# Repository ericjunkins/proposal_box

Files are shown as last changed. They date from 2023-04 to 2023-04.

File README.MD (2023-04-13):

# Proposal Box

<p float="left">
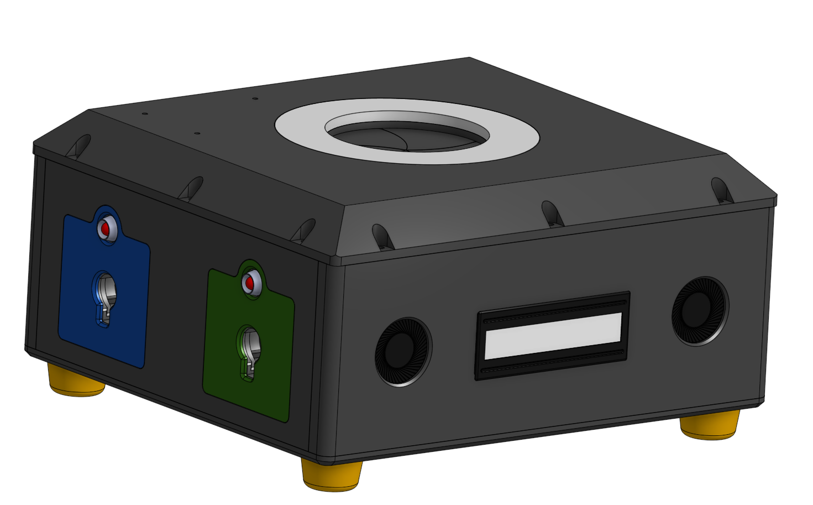
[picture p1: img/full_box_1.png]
  
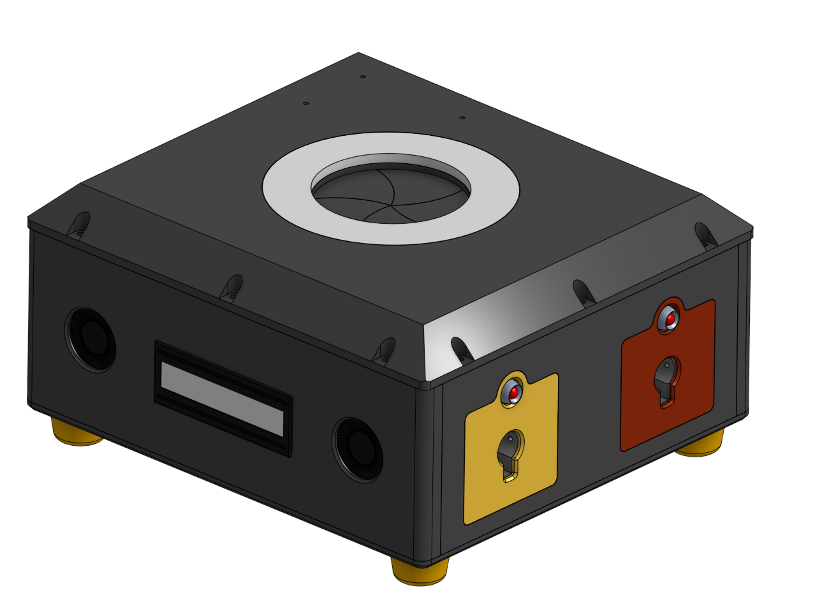
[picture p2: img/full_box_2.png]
   
</p>

<p float="left">
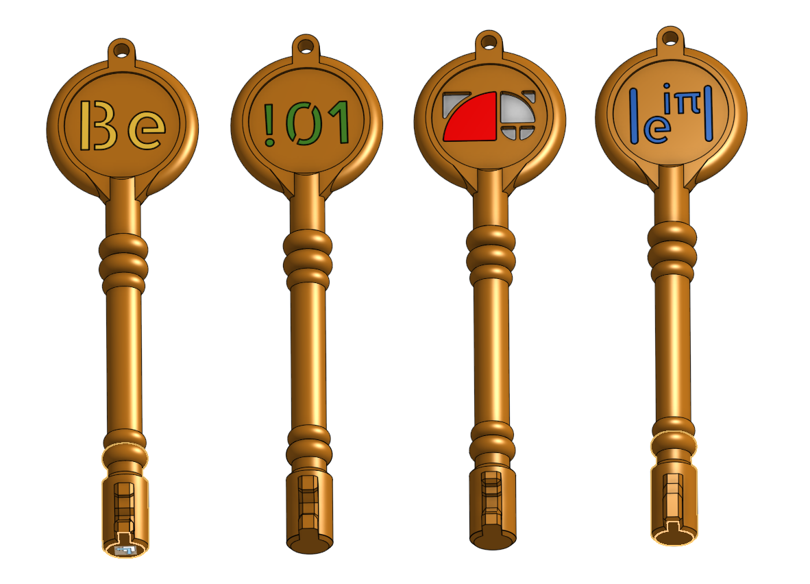
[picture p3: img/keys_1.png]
  
</p>

## Electrical Design

The design consists of 3 custom PCBs, alongside a set of electrical and mechanical parts to accomplish the motion, and user interaction desired.

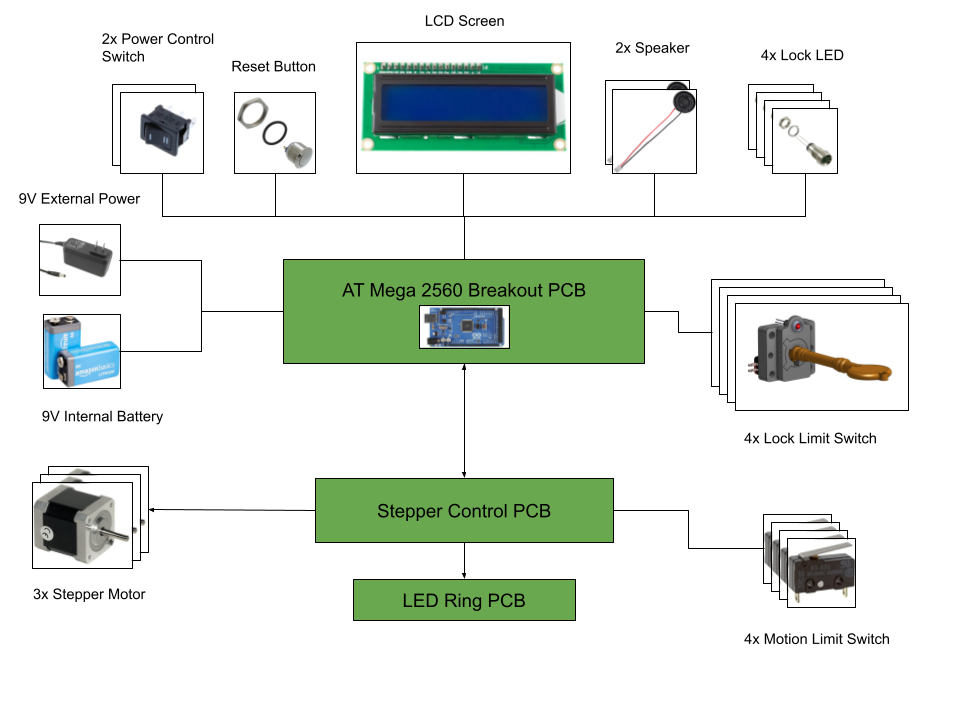
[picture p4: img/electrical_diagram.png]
Electrical Diagram


Full schematics, gerber files, and design files can be found in [electrical design folder](electrical_design/)
<p float="left">
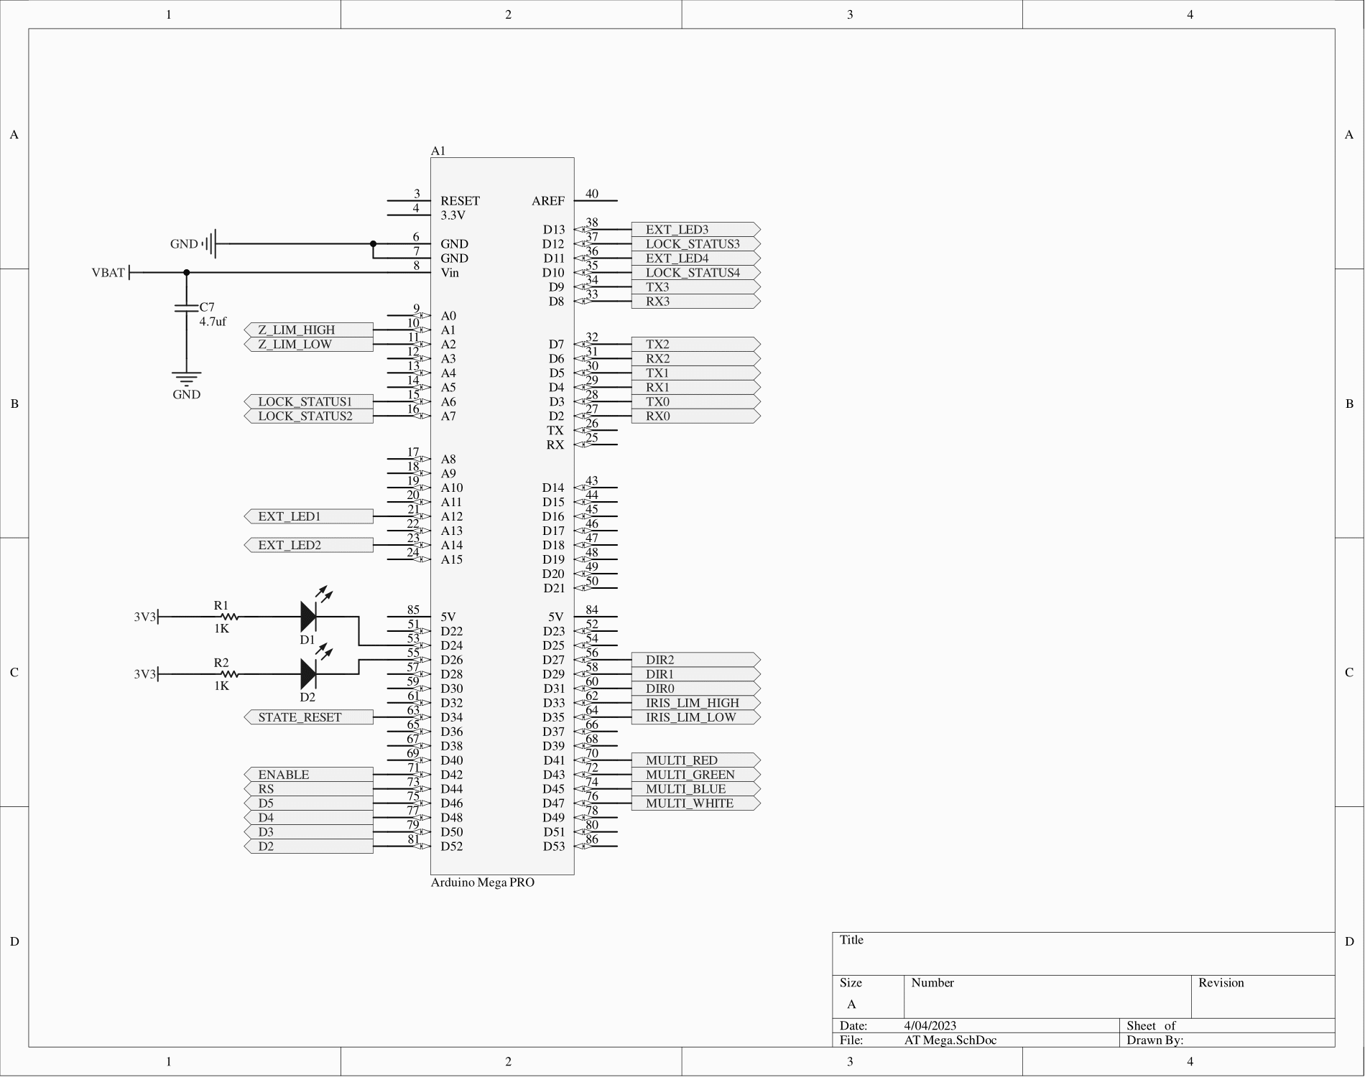
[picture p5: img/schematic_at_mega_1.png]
  
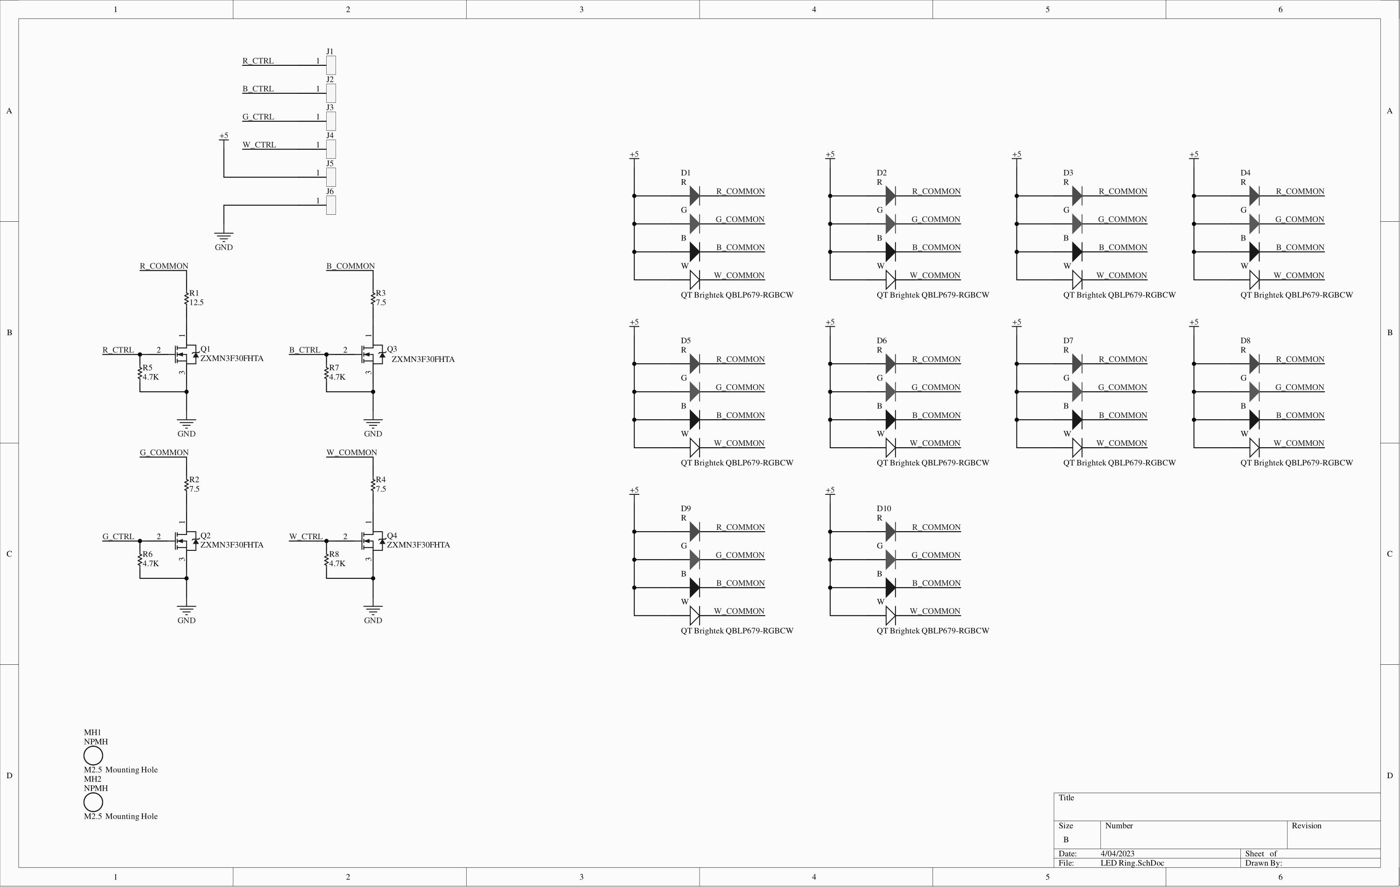
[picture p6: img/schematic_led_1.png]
   
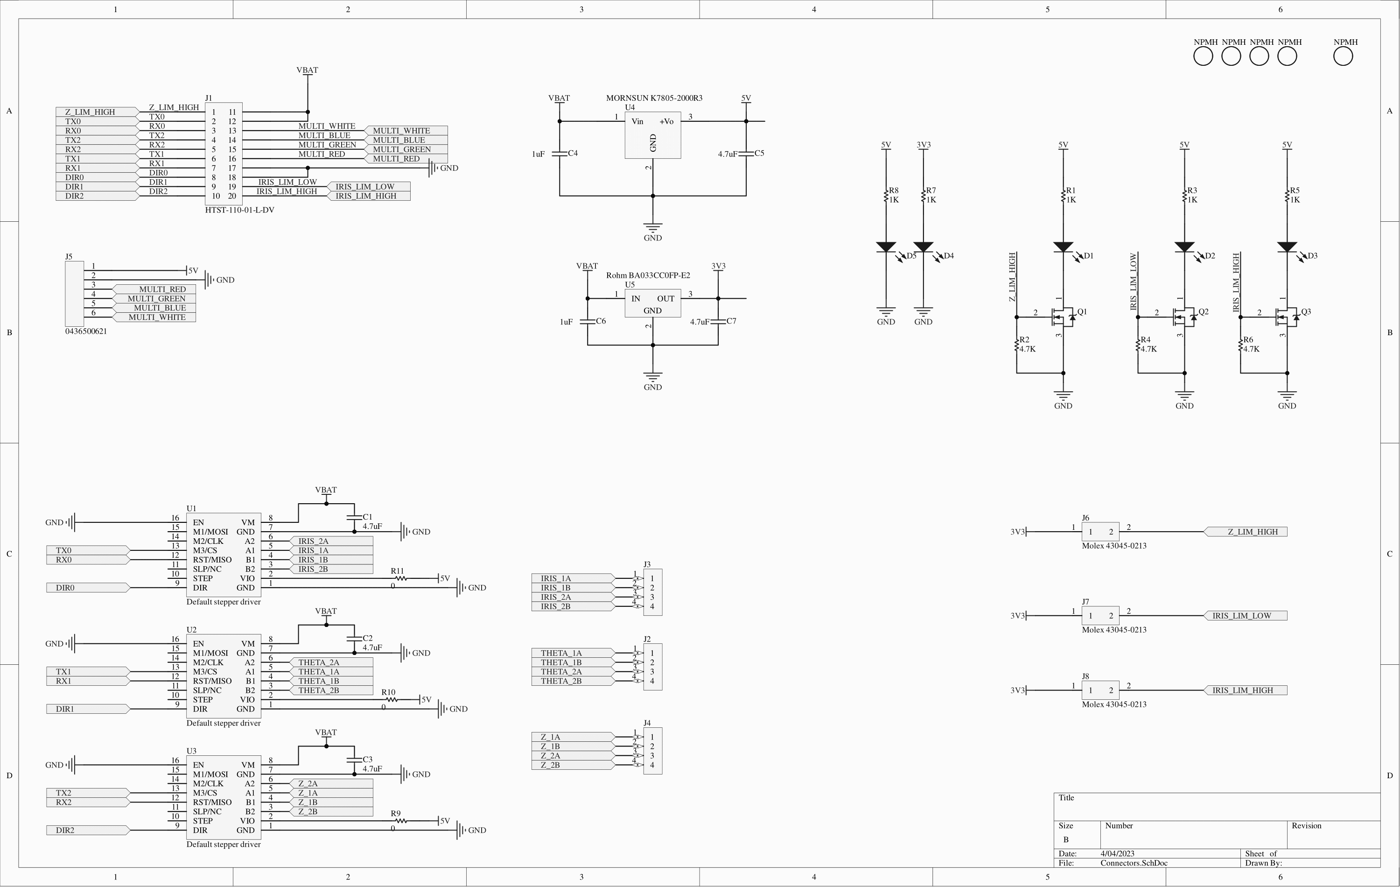
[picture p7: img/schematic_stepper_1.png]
   
</p>

## Mechanical Design

The CAD design of the project can be found at: https://cad.onshape.com/documents/44e33e8e96f078937c0840d5/w/a803ee7c0c0ba1d54d61a190/e/53a78a30a7107b3de1d018e0

### Structure

<p float="left">
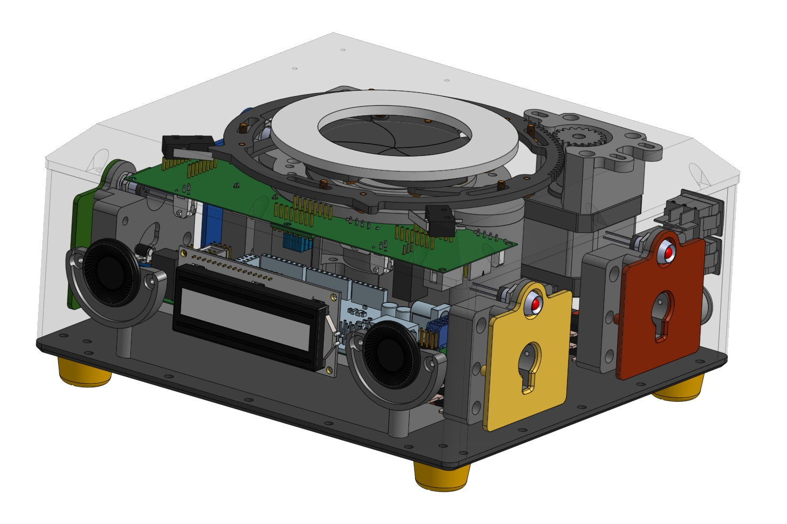
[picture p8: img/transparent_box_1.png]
  
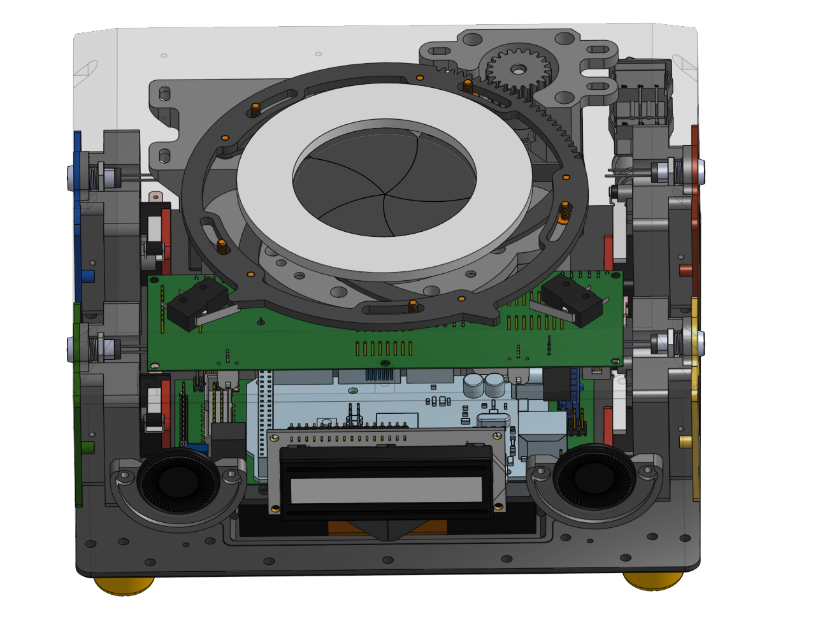
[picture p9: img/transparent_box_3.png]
   
</p>

## Iris
<p float="left">
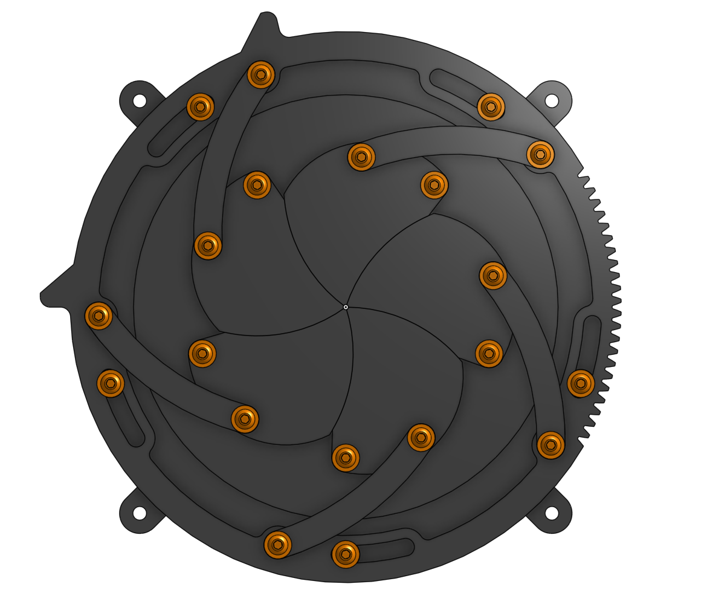
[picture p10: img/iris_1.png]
  
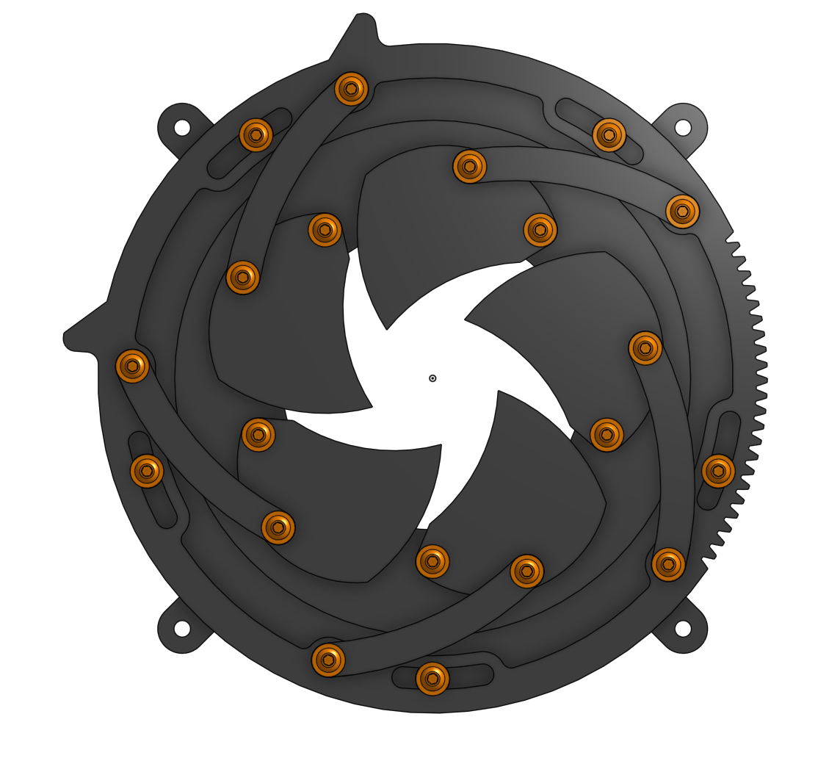
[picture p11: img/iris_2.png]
   
</p>

## Locks

<p float="left">
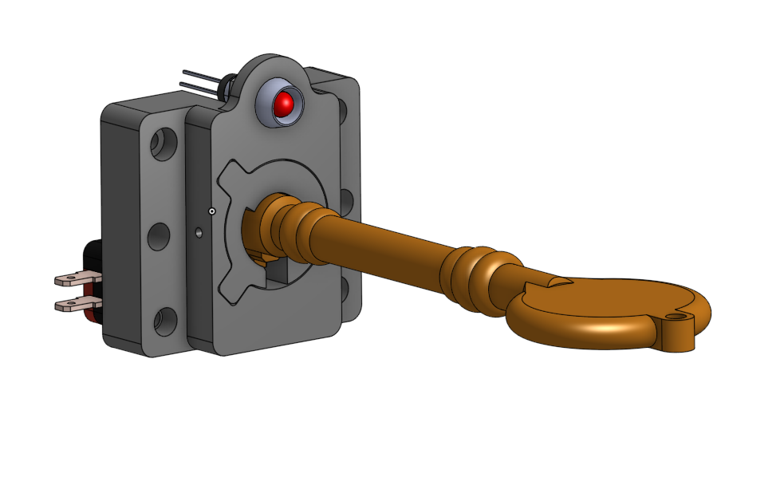
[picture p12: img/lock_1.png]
  
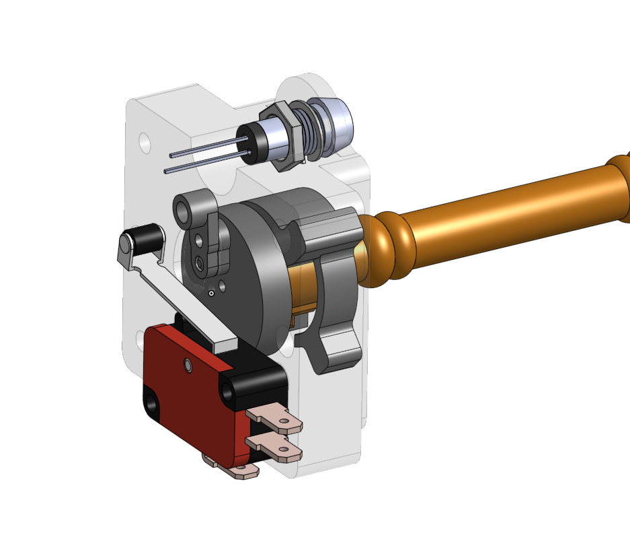
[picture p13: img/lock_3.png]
   
</p>

## BOM

Bill of Materials can be found in the [BOM Folder](BOM/)

## Software

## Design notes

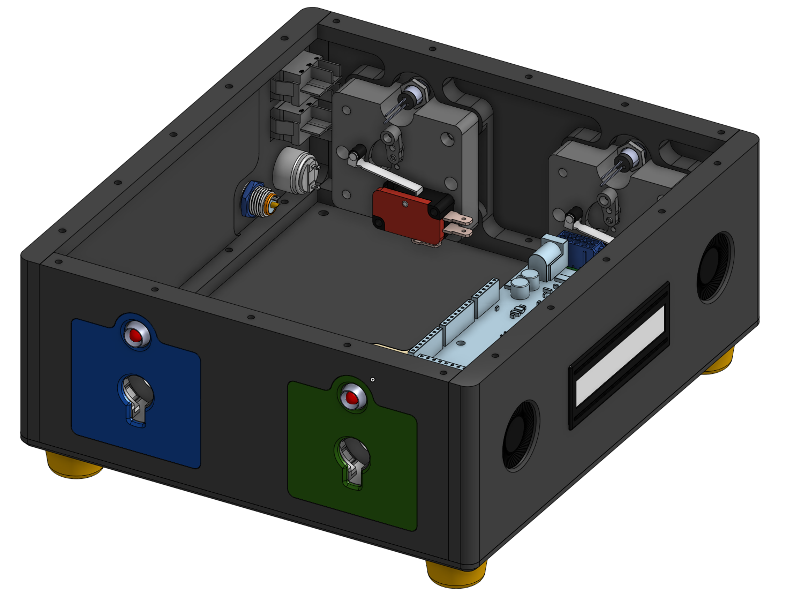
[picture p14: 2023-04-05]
img/bottom_2.png

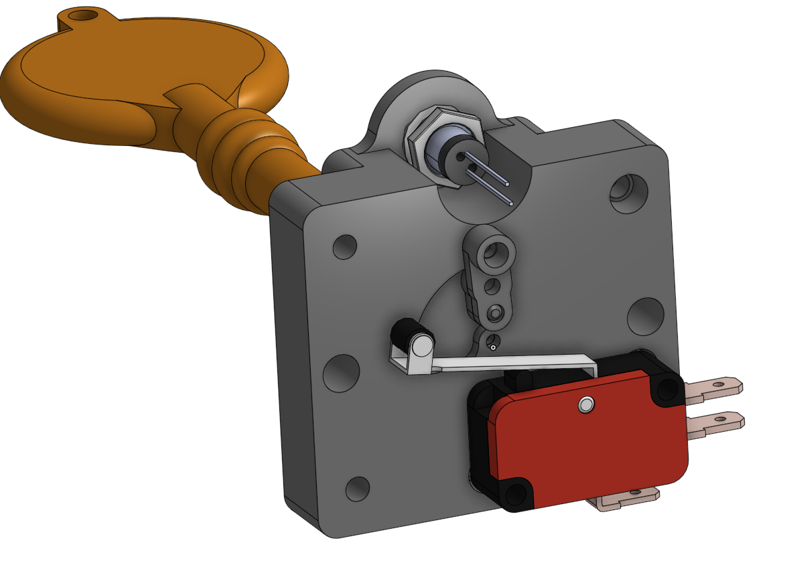
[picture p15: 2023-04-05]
img/lock 2.png

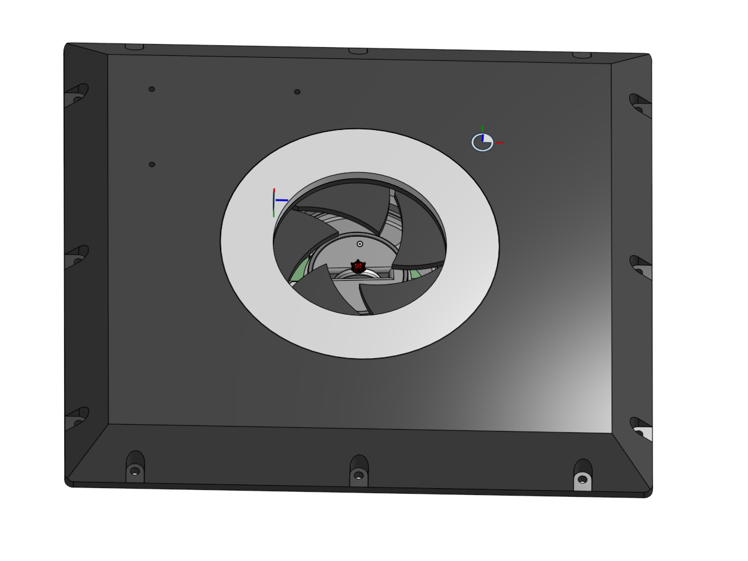
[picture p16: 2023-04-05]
img/lid_3.png

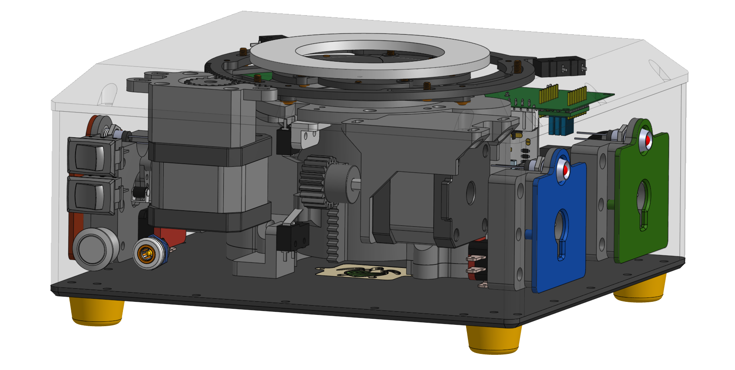
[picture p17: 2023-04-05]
img/transparent_box_2.png

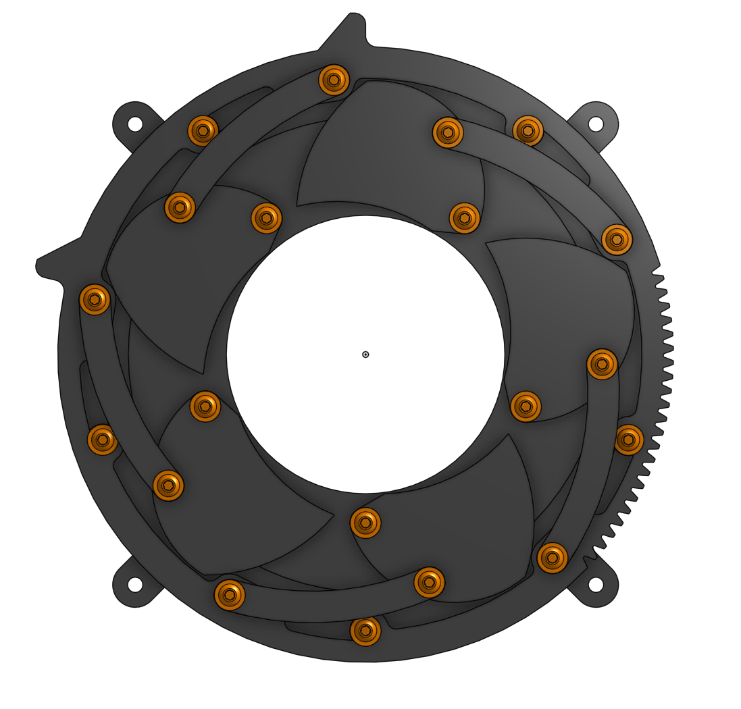
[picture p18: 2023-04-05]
img/iris_3.png

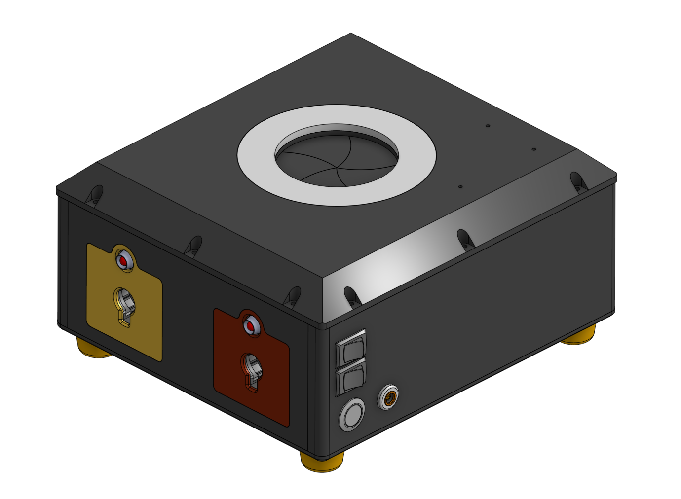
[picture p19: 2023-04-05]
img/full_box_3.png

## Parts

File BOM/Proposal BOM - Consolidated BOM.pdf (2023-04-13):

Part Type | Vendor | Quantity Part Number | Manufacturer Part Number Description | Customer Reference | Unit Price | Extended Price USD | Material | Finish | Color | Link PCB | Digikey | 10 ZXMN3F30FHCT-ND | ZXMN3F30FHTA | MOSFET N-CH 30V 3.8A SOT23-3 | Q1, Q2, Q3, Q4 | $0.47 | $4.70 N/A | N/A | N/A | N/A
PCB | Digikey | 10 1516-QBLP679-RGBCWCT-ND QBLP679-RGBCW | LED RGBW DIFFUSED 8PLCC SMD
D1, D2, D3, D4, D5, D6, D7, D8, D9, D10 | $0.49 | $4.93 N/A | N/A | N/A | N/A
PCB | Digikey | 10 A130138CT-ND | CRGCQ0805J4K7 | RES 4.7K OHM 5% 1/8W 0805 | R1, R2, R3, R4 | $0.04 | $0.38 N/A | N/A | N/A | N/A
PCB | Digikey | 10 A130132CT-ND | CRGCQ0805J470R | RES 470 OHM 5% 1/8W 0805 | R5, R6, R7, R8 | $0.03 | $0.32 N/A | N/A | N/A | N/A
PCB | Digikey | 1 SAM10529-ND | HTST-110-01-L-DV | CONN HEADER SMD 20POS 2.54MM | J1 | $4.37 | $4.37 N/A | N/A | N/A | N/A
PCB | Digikey | 1 WM20166CT-ND | 0436500621 | CONN HEADER SMD 6POS 3MM | J5 | $3.33 | $3.33 N/A | N/A | N/A | N/A
PCB | Digikey | 1 2725-K7805-2000R3-ND | K7805-2000R3 | DC DC CONVERTER 5V 10W | U4 | $7.11 | $7.11 N/A | N/A | N/A | N/A
PCB | Digikey | 1 BA033CC0FP-E2CT-ND | BA033CC0FP-E2 | IC REG LINEAR 3.3V 1A TO252-3 | U5 | $1.41 | $1.41 N/A | N/A | N/A | N/A
PCB | Digikey | 6 SSW-108-01-T-S-LL-ND | SSW-108-01-T-S-LL | CONN RCPT 8POS 0.1 TIN PCB | U1, U2, U3 | $1.47 | $8.82 N/A | N/A | N/A | N/A
PCB | Digikey | 3 WM1919-ND | 0436500415 | CONN HEADER VERT 4POS 3MM | J2, J3, J4 | $1.28 | $3.84 N/A | N/A | N/A | N/A
PCB | Digikey | 3 WM2648-ND | 0430450213 | CONN HEADER VERT 2POS | J6, J7, J8 | $1.21 | $3.63 N/A | N/A | N/A | N/A
PCB | Digikey | 3 ZXMN3F30FHCT-ND | ZXMN3F30FHTA | MOSFET N-CH 30V 3.8A SOT23-3 | Q1, Q2, Q3 | $0.47 | $1.41 N/A | N/A | N/A | N/A
PCB | Digikey | 10 A130138CT-ND | CRGCQ0805J4K7 | RES 4.7K OHM 5% 1/8W 0805 | R1, R3, R5, R7, R8 | $0.04 | $0.38 N/A | N/A | N/A | N/A
PCB | Digikey | 10 A130132CT-ND | CRGCQ0805J470R | RES 470 OHM 5% 1/8W 0805 | R2, R4, R6 | $0.03 | $0.32 N/A | N/A | N/A | N/A
PCB | Digikey | 10 RMCF0805ZT0R00CT-ND | RMCF0805ZT0R00 | RES 0 OHM JUMPER 1/8W 0805 | R9, R10, R11 | $0.02 | $0.18 N/A | N/A | N/A | N/A
PCB | Digikey | 10 1276-1244-1-ND | CL21A475KAQNNNE | CAP CER 4.7UF 25V X5R 0805 | C1, C2, C3, C5, C7 | $0.07 | $0.73 N/A | N/A | N/A | N/A
PCB | Digikey | 10 1276-1066-1-ND | CL21B105KAFNNNE | CAP CER 1UF 25V X7R 0805 | C4, C6 | $0.07 | $0.65 N/A | N/A | N/A | N/A
PCB | Digikey | 10 160-1423-1-ND | LTST-C171GKT | LED GREEN CLEAR CHIP SMD | D1, D2, D3, D4, D5 | $0.14 | $1.41 N/A | N/A | N/A | N/A
PCB | Digikey | 10 A130135CT-ND | CRGCQ0805J1K5 | RES 1.5K OHM 5% 1/8W 0805 | R1, R2, R3, R4, R5 | $0.04 | $0.38 N/A | N/A | N/A | N/A
PCB | Digikey | 10 13-RC0805FR-13220RLCT-ND RC0805FR-13220RL | RES 220 OHM 1% 1/8W 0805 | R10, R12, R16, R17, R21 | $0.03 | $0.25 N/A | N/A | N/A | N/A
PCB | Digikey | 10 A130138CT-ND | CRGCQ0805J4K7 | RES 4.7K OHM 5% 1/8W 0805
R6, R7, R8, R9, R13, R14, R15, R18, R19, R22 | $0.04 | $0.38 N/A | N/A | N/A | N/A
PCB | Digikey | 10 RMCF0805ZT0R00CT-ND | RMCF0805ZT0R00 | RES 0 OHM JUMPER 1/8W 0805 | C5, C6 | $0.02 | $0.18 N/A | N/A | N/A | N/A
PCB | Digikey | 10 1276-1066-1-ND | CL21B105KAFNNNE | CAP CER 1UF 25V X7R 0805 | C1, C3, C8, C10 | $0.07 | $0.65 N/A | N/A | N/A | N/A
PCB | Digikey | 10 1276-1244-1-ND | CL21A475KAQNNNE | CAP CER 4.7UF 25V X5R 0805 | C7, C9, C11 | $0.07 | $0.73 N/A | N/A | N/A | N/A
PCB | Digikey | 10 1276-1096-1-ND | CL21A106KOQNNNE | CAP CER 10UF 16V X5R 0805 | C2, C4 | $0.07 | $0.74 N/A | N/A | N/A | N/A
PCB | Digikey | 10 160-1423-1-ND | LTST-C171GKT | LED GREEN CLEAR CHIP SMD | D1, D2, D3, D4 | $0.14 | $1.41 N/A | N/A | N/A | N/A
PCB | Digikey | 1 1738-1041-ND | DFR0299 | DFPLAYER - A MINI MP3 PLAYER | U1 | $5.90 | $5.90 N/A | N/A | N/A | N/A
PCB | Digikey | 1 PAM8406DRDICT-ND | PAM8406DR | IC AMP D/AB STEREO 5W 16SOP | U2 | $0.85 | $0.85 N/A | N/A | N/A | N/A
PCB | Digikey | 1 WM1793-ND | 0430451012 | CONN HEADER VERT 10POS 3MM | J13 | $2.60 | $2.60 N/A | N/A | N/A | N/A
PCB | Digikey | 1 2725-K7805-2000R3-ND | K7805-2000R3 | DC DC CONVERTER 5V 10W | U3 | $7.11 | $7.11 N/A | N/A | N/A | N/A
PCB | Digikey | 1 BA033CC0FP-E2CT-ND | BA033CC0FP-E2 | IC REG LINEAR 3.3V 1A TO252-3 | U4 | $1.41 | $1.41 N/A | N/A | N/A | N/A
PCB | Digikey | 1 2057-PH1-12-UA-ND | PH1-12-UA | CONN HEADER VERT 12POS 2.54MM | J12 | $0.20 | $0.20 N/A | N/A | N/A | N/A
PCB | Digikey | 2 SAM8996-ND | TSW-104-07-F-D | CONN HEADER VERT 8POS 2.54MM | J5, J7 | $0.97 | $1.94 N/A | N/A | N/A | N/A
PCB | Digikey | 3 732-5315-ND | 61300211121 | CONN HEADER VERT 2POS 2.54MM | J1, J2, J9 | $0.13 | $0.39 N/A | N/A | N/A | N/A
PCB | Digikey | 1 SAM10529-ND | HTST-110-01-L-DV | CONN HEADER SMD 20POS 2.54MM | J6 | $4.37 | $4.37 N/A | N/A | N/A | N/A
PCB | Digikey | 2 1034-ZXMN3F31DN8CT-ND | ZXMN3F31DN8TA | MOSFET 2N-CH 30V 5.7A 8SOIC | Q1, Q2 | $0.87 | $1.74 N/A | N/A | N/A | N/A
PCB | Digikey | 1 1050-1018-ND | A000067 | ARDUINO MEGA2560 ATMEGA2560 | A1 | $48.40 | $48.40 N/A | N/A | N/A | N/A
PCB | Digikey | 1 2553-2044-2X18G00SA-ND | 2044-2X18G00SA | PCB SOCKET, DOUBLE ROW, 36 PIN, | A1 | $1.00 | $1.00 N/A | N/A | N/A | N/A
PCB | Digikey | 10 SSW-108-01-T-S-LL-ND | SSW-108-01-T-S-LL | CONN RCPT 8POS 0.1 TIN PCB | A1, U2 | $1.28 | $12.82 N/A | N/A | N/A | N/A
PCB | Digikey | 1 CT-9EW103-ND | CT-9EW103 | TRIMMER 10K OHM 0.5W PC PIN TOP | R20 | $2.07 | $2.07 N/A | N/A | N/A | N/A Machine Part | Alibaba | 5 N/A | N/A | Iris_leaf | N/A | $14.00 | $70.00 Aluminum 6061 | Type 2 Annodize | Black | N/A Machine Part | Alibaba | 1 N/A | N/A | Iris_base | N/A | $36.50 | $36.50 Aluminum 6061 | Type 2 Annodize | Black | N/A Machine Part | Alibaba | 1 N/A | N/A | Spur_gear | N/A | $46.50 | $46.50 Aluminum 6061 | Type 2 Annodize | Black | N/A Machine Part | Alibaba | 1 N/A | N/A | Lock_cover | N/A | $21.50 | $21.50 Aluminum 6061 | Type 2 Annodize | Red | N/A Machine Part | Alibaba | 1 N/A | N/A | Lock_cover | N/A | $21.50 | $21.50 Aluminum 6061 | Type 2 Annodize | Blue | N/A Machine Part | Alibaba | 1 N/A | N/A | Lock_cover | N/A | $21.50 | $21.50 Aluminum 6061 | Type 2 Annodize | Green | N/A Machine Part | Alibaba | 1 N/A | N/A | Lock_cover | N/A | $21.50 | $21.50 Aluminum 6061 | Type 2 Annodize | Yellow | N/A Machine Part | Alibaba | 1 N/A | N/A | Back_plate | N/A | $24.00 | $24.00 Aluminum 6061 | Type 2 Annodize | Black | N/A Machine Part | Alibaba | 1 N/A | N/A | Bottom_plate | N/A | $23.00 | $23.00 Aluminum 6061 | Type 2 Annodize | Black | N/A Machine Part | Alibaba | 1 N/A | N/A | Front_plate | N/A | $33.00 | $33.00 Aluminum 6061 | Type 2 Annodize | Black | N/A Machine Part | Alibaba | 1 N/A | N/A | Lid_plate | N/A | $100.00 | $100.00 Aluminum 6061 | Type 2 Annodize | Black | N/A Machine Part | Alibaba | 2 N/A | N/A | Side_plate | N/A | $25.00 | $50.00 Aluminum 6061 | Type 2 Annodize | Black | N/A
3D Printed | JLCPCB | 6 N/A | N/A | Lock Housing - Bar | N/A | $1.00 | $6.00 Black Resin | Sanding | Matte Black | N/A
3D Printed | JLCPCB | 2 N/A | N/A | Key 1 Static | N/A | $1.00 | $2.00 Black Resin | Sanding | Matte Black | N/A
3D Printed | JLCPCB | 2 N/A | N/A | Key 2 Static | N/A | $1.00 | $2.00 Black Resin | Sanding | Matte Black | N/A
3D Printed | JLCPCB | 2 N/A | N/A | Key 3 Static | N/A | $1.00 | $2.00 Black Resin | Sanding | Matte Black | N/A
3D Printed | JLCPCB | 2 N/A | N/A | Key 4 Static | N/A | $1.00 | $2.00 Black Resin | Sanding | Matte Black | N/A
3D Printed | JLCPCB | 5 N/A | N/A | Lock Housing - Tumbler 0 | N/A | $1.00 | $5.00 Black Resin | Sanding | Matte Black | N/A
3D Printed | JLCPCB | 6 N/A | N/A | Lock Housing | N/A | $6.21 | $37.27 Black Resin | Sanding | Matte Black | N/A
3D Printed | JLCPCB | 1 N/A | N/A | Ring Coupler | N/A | $1.64 | $1.64 Black Resin | Sanding | Matte Black | N/A
3D Printed | JLCPCB | 1 N/A | N/A | Iris Stepper Block | N/A | $3.94 | $3.94 Black Resin | Sanding | Matte Black | N/A
3D Printed | JLCPCB | 1 N/A | N/A | Center Block | N/A | $17.05 | $17.05 Black Resin | Sanding | Matte Black | N/A
3D Printed | JLCPCB | 1 N/A | N/A | Ring Mount | N/A | $2.95 | $2.95 Black Resin | Sanding | Matte Black | N/A
3D Printed | JLCPCB | 3 N/A | N/A | Bearing Clamp | N/A | $1.90 | $5.71 Black Resin | Sanding | Matte Black | N/A
3D Printed | JLCPCB | 2 N/A | N/A | Upper Z Lim Bracket | N/A | $1.00 | $2.00 Black Resin | Sanding | Matte Black | N/A
3D Printed | JLCPCB | 7 N/A | N/A | Iris Linkage | N/A | $1.00 | $7.00 Black Resin | Sanding | Matte Black | N/A
3D Printed | JLCPCB | 1 N/A | N/A | Battery Cover | N/A | $2.01 | $2.01 Black Resin | Sanding | Matte Black | N/A
3D Printed | JLCPCB | 1 N/A | N/A | Z Shaft Bottom Bracket | N/A | $1.35 | $1.35 Black Resin | Sanding | Matte Black | N/A
3D Printed | JLCPCB | 1 N/A | N/A | Lower Z Lim Bracket | N/A | $2.25 | $2.25 Black Resin | Sanding | Matte Black | N/A
3D Printed | JLCPCB | 1 N/A | N/A | Z Stepper Block | N/A | $5.71 | $5.71 Black Resin | Sanding | Matte Black | N/A
3D Printed | JLCPCB | 1 N/A | N/A | Shaft Mounting Block | N/A | $5.08 | $5.08 Black Resin | Sanding | Matte Black | N/A
3D Printed | JLCPCB | 1 N/A | N/A | Z Carriage | N/A | $10.76 | $10.76 Black Resin | Sanding | Matte Black | N/A
3D Printed | JLCPCB | 1 N/A | N/A | Diffuser Mount | N/A | $1.00 | $1.00 Black Resin | Sanding | Matte Black | N/A
Laser Cut | SendcutSend | 1 N/A | N/A | Lid_Upper_Plate | N/A | $52.48 | $52.48 5052 Aluminum (0.125") Black | Annodize Type 2 | N/A
Laser Cut | SendcutSend | 1 N/A | N/A | Diffuser | N/A | $3.20 | $3.20 Acrylic-White (0.118") | Clear | None | N/A
Laser Cut | SendcutSend | 1 N/A | N/A | Upper Cosmetic Ring | N/A | $7.02 | $7.02 5052 Aluminum (0.125") White | Gloss White Powder Coat N/A Misc | Amazon | 1 N/A | N/A | Black Velvet Felt | N/A | $12.99 | $12.99 N/A | N/A | N/A | https://www.amazon.com/dp/B08TMTM1ZT?psc=1&ref=ppx_yo2ov_dt_b_product_details PCB | Amazon | 1 N/A | N/A | TMC2209 Stepper Driver 5PCS | N/A | $29.99 | $29.99 N/A | N/A | N/A | https://www.amazon.com/dp/B07ZQ3C1XW?psc=1&ref=ppx_yo2ov_dt_b_product_details Electronics | Amazon | 1 N/A | N/A | JJHXSM Magnetic Loudspeaker 4PCS | N/A | $8.99 | $8.99 N/A | N/A | N/A | https://www.amazon.com/dp/B09HGTKXC4?psc=1&ref=ppx_yo2ov_dt_b_product_details Misc | Amazon | 5 N/A | N/A | WEICHUAN Metal Antique Bronze Keychain | N/A | $5.99 | $29.95 N/A | N/A | N/A | https://www.amazon.com/gp/product/B01N3VRYV7/ref=ppx_yo_dt_b_asin_title_o03_s00?ie=UTF8&psc=1
Electronics | Amazon | 1 N/A | N/A
STEPPERONLINE Short Body Nema 17 Bipolar Stepper Motor 1A 22.6 oz.in/16Ncm DIY CNC Extruder | N/A | $11.99 | $11.99 N/A | N/A | N/A | https://www.amazon.com/gp/product/B00PNEQ79Q/ref=ppx_yo_dt_b_asin_title_o03_s00?ie=UTF8&psc=1
Electronics | Amazon | 1 N/A | N/A
[3pcs of Pack] Nema17 Stepper Motor, 2Phase 4 Lead 42-34 Stepping Motor with 1m Cable 42BYGH 34MM 1.5A (17HS4401S) for CR-10, Ender 3, Anet A8, Anycubic Mega Series 3D Printers and CNC Extruder N/A | $29.99 | $29.99 N/A | N/A | N/A | https://www.amazon.com/gp/product/B09JFGSS8H/ref=ppx_yo_dt_b_search_asin_title?ie=UTF8&th=1 Misc | Amazon | 1 N/A | N/A
| | | | ZIRO Silk PLA Filament 1.75mm,3D Printer Filament PLA Silky Series 1.75mm 1KG(2.2lbs),Bronze | N/A | $21.99 | $21.99 N/A | N/A | N/A | https://www.amazon.com/dp/B08BG4VHF4?ref=ppx_yo2ov_dt_b_product_details&th=1
Structure | McMaster Carr | 1 N/A | N/A | Unthreaded Bumper 10PCS | N/A | $7.42 | $7.42 N/A | N/A | N/A | https://www.mcmaster.com/catalog/9540K913
Structure | McMaster Carr | 2 N/A | N/A | Metal Gear - 20 Degree Pressure Angle | N/A | $15.52 | $31.04 N/A | N/A | N/A | https://www.mcmaster.com/2664N353/
Structure | McMaster Carr | 1 N/A | N/A
18-8 Stainless Steel Flanged Button Head Screw M3 x 0.5 mm Thread Size, 6 mm Long | N/A | $5.04 | $5.04 N/A | N/A | N/A | https://www.mcmaster.com/97654A674/ Electronics | Digikey | 1 N/A | N/A | AC/DC WALL MOUNT ADAPTER 9V 18W | N/A | $13.66 | $13.66 N/A | N/A | N/A | https://www.digikey.com/en/products/detail/xp-power/VEL18US090-US-JA/5864666
Electronics | Digikey | 1 N/A | N/A | CONN JACK PNL MNT 5.5X2.1MM ISO | N/A | $4.92 | $4.92 N/A | N/A | N/A | https://www.digikey.com/en/products/detail/tensility-international-corp/54-00151/9829987
Electronics | Digikey | 4 N/A | N/A | PNL MNT W/ WIRE 568NM 25MCD GRN | N/A | $3.03 | $12.12 N/A | N/A | N/A | https://www.digikey.com/en/products/detail/bivar-inc/MPR5GD/3488863
Electronics | Digikey | 1 N/A | N/A | SWITCH PUSHBUTTON SPST-NO 2A 48V | N/A | $6.37 | $6.37 N/A | N/A | N/A | https://www.digikey.com/en/products/detail/e-switch/PV2F240NN/4028687?s=N4IgTCBcDaIKIHECsBOAzEgtAOQCIgF0BfIA
Electronics | Digikey | 2 N/A | N/A | SWITCH ROCKER SPDT ON-ON W/PRINT | N/A | $2.12 | $4.24 N/A | N/A | N/A | https://www.digikey.com/en/products/detail/switch-components/RF1-1D-DC-2-B-4/11492757
Electronics | Digikey | 1 N/A | N/A | IDC CABLE - MKC20A/MC20G/MKC20A | N/A | $5.19 | $5.19 N/A | N/A | N/A | https://www.digikey.com/en/products/detail/3m/M3CCA-2006J/230139
Structure | Gobilda | 20 N/A | N/A | 2101 Series Stainless Steel D-Shaft (6mm Diameter, 80mm Length) | N/A | $2.29 | $45.80 N/A | N/A | N/A | https://www.gobilda.com/2101-series-stainless-steel-d-shaft-6mm-diameter-80mm-length/
Electronics | Amazon | 1 N/A | N/A | LP 9V Rechargeable Battery Charger Pack, 4 Pack 600mah 9 Volt Batteries | N/A | $27.98 | $27.98 N/A | N/A | N/A | https://www.amazon.com/gp/product/B07RT332DY/ref=ppx_yo_dt_b_asin_title_o06_s00?ie=UTF8&th=1
Structure | Amazon | 1 N/A | N/A
RuiLing 4pcs 9V Battery Holder Box with 2X Lead Wire Spring Clip DIY Plastic Cell Batteries Container | N/A | $8.99 | $8.99 N/A | N/A | N/A | https://www.amazon.com/gp/product/B07Q1N2MHT/ref=ppx_yo_dt_b_asin_title_o05_s00?ie=UTF8&psc=1
Electronics | Amazon | 1 N/A | N/A
BUYGOO 6Pcs V-156-1C25 Micro Limit Switch with Hinge Roller Momentary SPDT Snap Action for Arduino CYT1046 | N/A | $7.79 | $7.79 N/A | N/A | N/A | https://www.amazon.com/gp/product/B07D9C2B6J/ref=ppx_yo_dt_b_asin_title_o08_s00?ie=UTF8&psc=1
Electronics | Amazon | 1 N/A | N/A
JANDECCN 20Pcs Limit Switch AC 5A 125 250V SPDT 1NO 1NC Short Straight Hinge Lever Arm Micro Switch KW12 (Type B) | N/A | $9.99 | $9.99 N/A | N/A | N/A | https://www.amazon.com/gp/product/B07X142VGC/ref=ppx_yo_dt_b_asin_image_o09_s00?ie=UTF8&psc=1

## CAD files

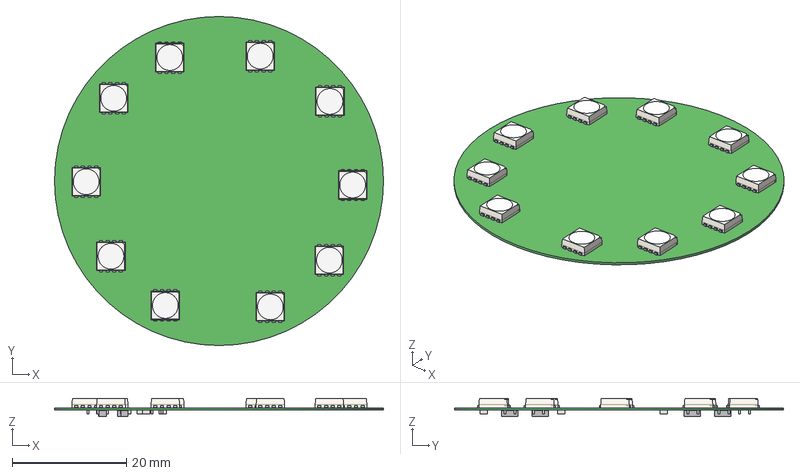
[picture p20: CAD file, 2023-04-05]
electrical_design/STEP/LED Ring.step
57.5 x 57.5 x 3.17 mm
Extruded x 20

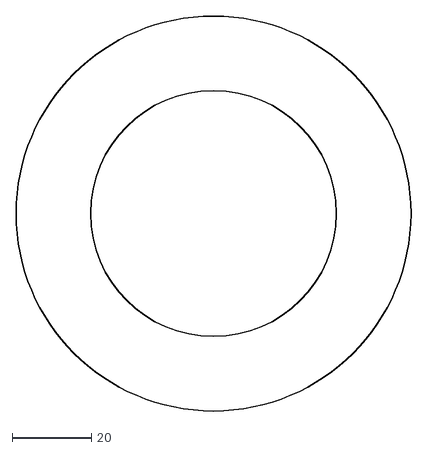
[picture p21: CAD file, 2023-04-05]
mechanical_design/DXF/Proposal_box - Upper cosmetic ring.dxf
99.6 x 99.6

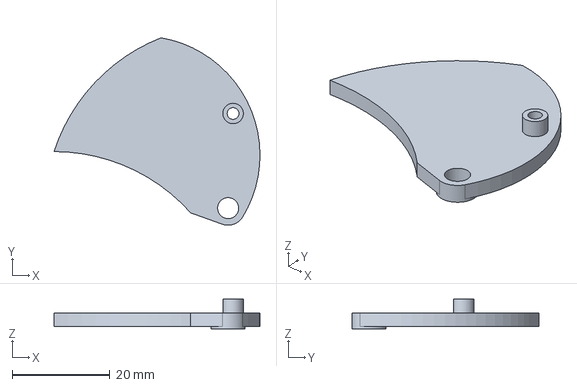
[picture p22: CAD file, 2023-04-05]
mechanical_design/STEP/Iris V2 - Leaf.step
42.2 x 38.4 x 6.05 mm

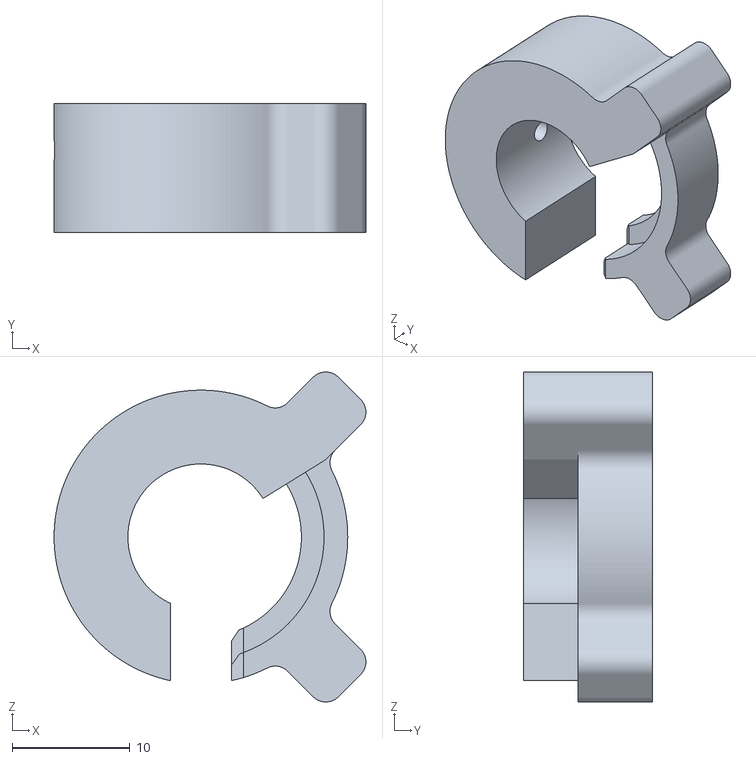
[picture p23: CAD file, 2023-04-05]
mechanical_design/STL/Key - Key 1 Static.stl
26.5 x 11.0 x 28.0

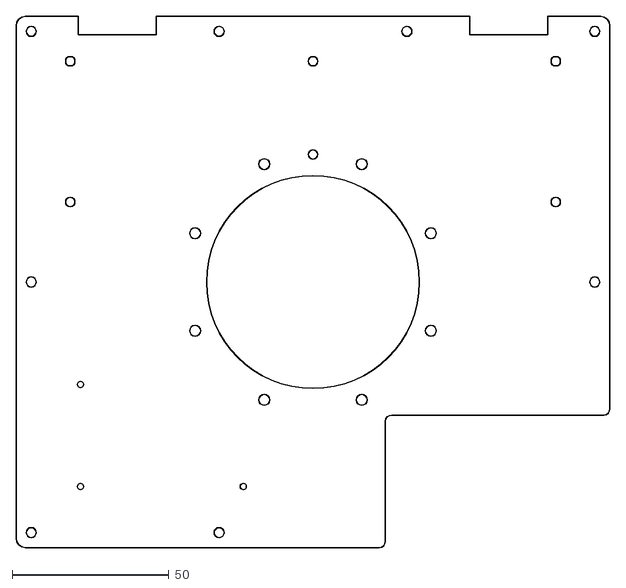
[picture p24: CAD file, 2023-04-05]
mechanical_design/DXF/Proposal_box - Upper Plate.dxf
189.6 x 169.6

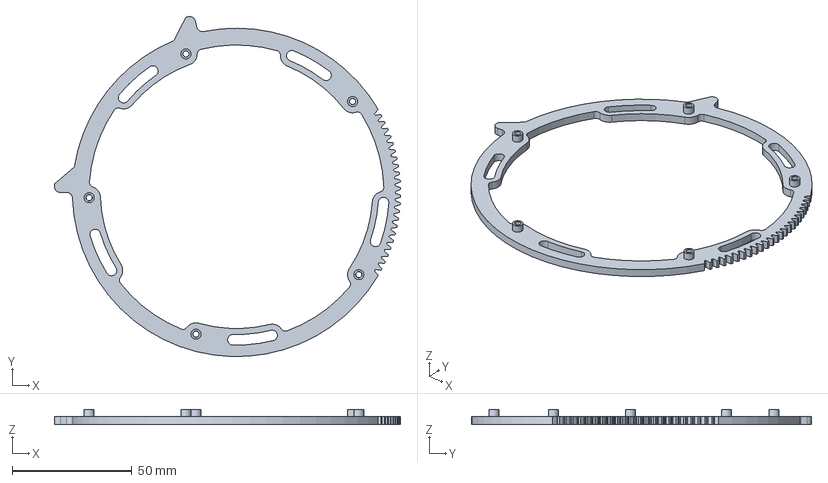
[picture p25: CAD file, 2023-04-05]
mechanical_design/STEP/Iris V2 - Spur gear (135 teeth).step
144.5 x 141.8 x 6.05 mm

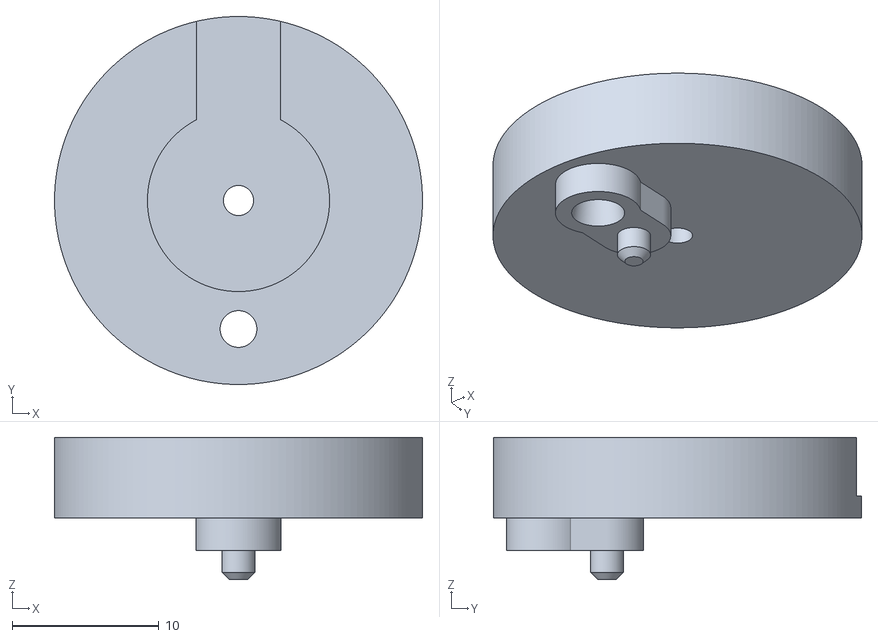
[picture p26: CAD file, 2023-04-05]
mechanical_design/STL/Lock Housing - Tumbler 0.stl
25.1 x 25.1 x 9.70

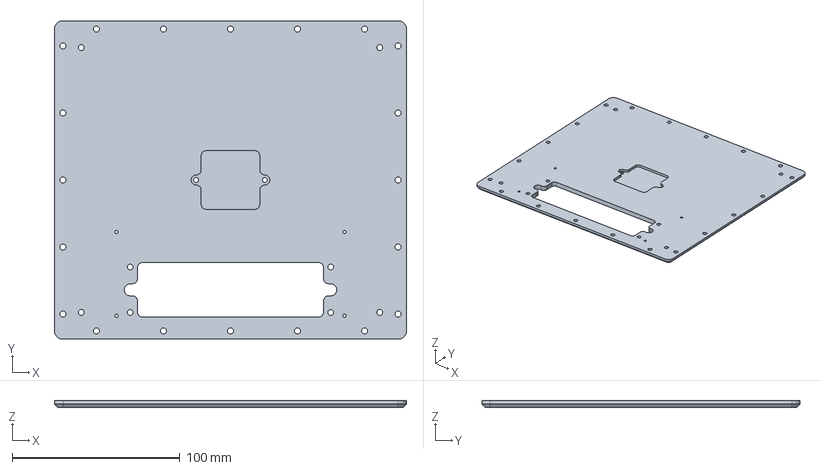
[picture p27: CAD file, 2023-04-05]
mechanical_design/STEP/Proposal_box - Machine_bottom_plate.step
210.0 x 190.0 x 4.00 mm

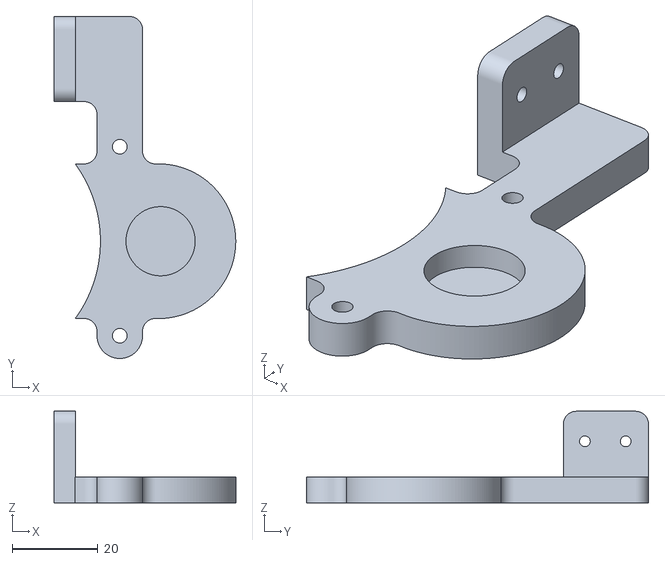
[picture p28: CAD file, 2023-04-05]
mechanical_design/STL/Proposal_box - Lower Limit Bracket.stl
42.2 x 79.6 x 21.3

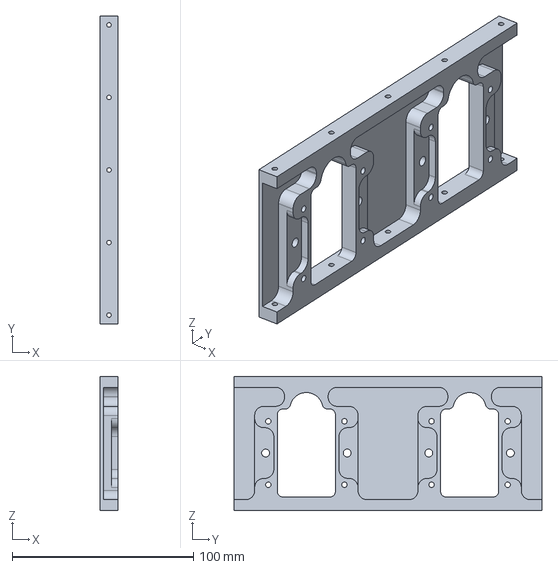
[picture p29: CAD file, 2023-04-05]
mechanical_design/STEP/Proposal_box - Machined_side_plate.step
10.0 x 169.8 x 74.0 mm

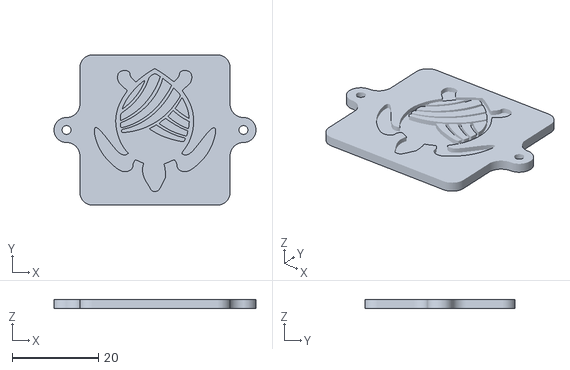
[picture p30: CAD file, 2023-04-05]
mechanical_design/STL/Proposal_box - Turtle_plate.stl
46.8 x 34.8 x 2.00

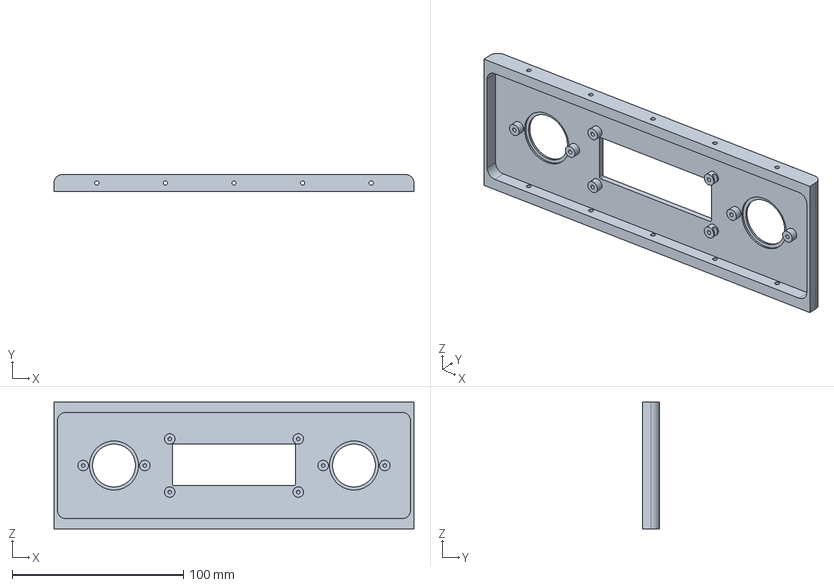
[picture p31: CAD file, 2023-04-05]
mechanical_design/STEP/Machine Front Plate.step
210.0 x 10.0 x 74.0 mm

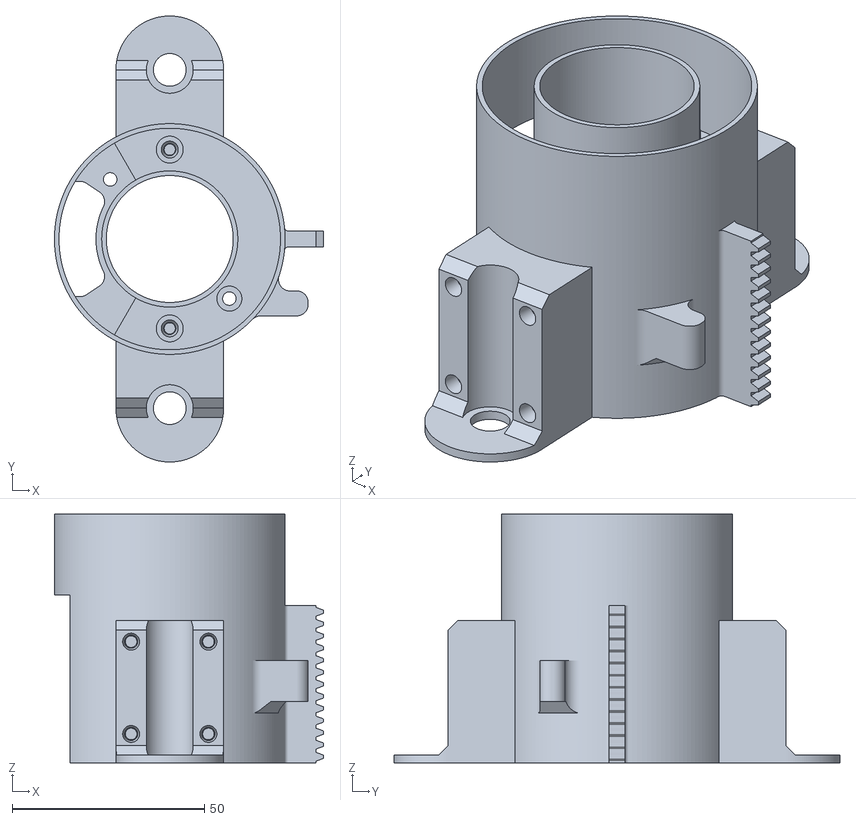
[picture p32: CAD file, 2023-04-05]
mechanical_design/STL/Ring Mount - Center Block.stl
70.0 x 116.0 x 64.6

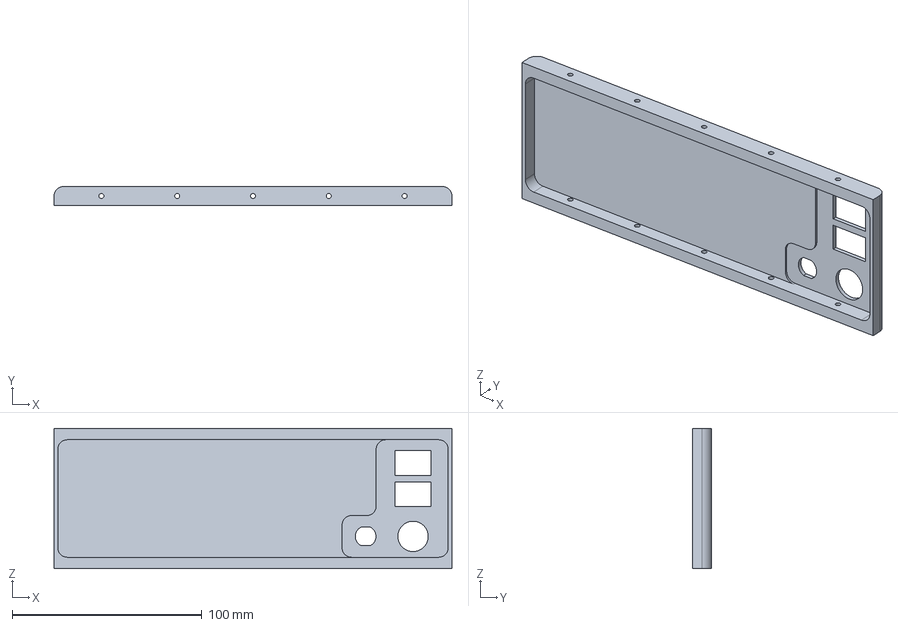
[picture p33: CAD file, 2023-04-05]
mechanical_design/STEP/Proposal_box - Machine_back_plate.step
210.0 x 10.0 x 74.0 mm

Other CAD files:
mechanical_design/STL/Proposal_box - Shaft Mounting Bracket.stl
mechanical_design/STEP/Proposal_box - Lock_cover blue.step
mechanical_design/STL/Ring Base - Ring Coupler.stl
mechanical_design/STEP/Iris V2 - Linkage.step
mechanical_design/STEP/Iris V2 - Base.step
mechanical_design/STL/Battery Clip Vertical - Cover Plate.stl
mechanical_design/STL/Iris V2 - Linkage.stl
mechanical_design/STL/Key - Key 2 Static.stl
mechanical_design/STL/Key - Key 3 Static.stl
mechanical_design/STL/Key - Key 4 Static.stl
mechanical_design/STL/Lid - Battery Holder.stl
mechanical_design/STL/Lock Housing - Bar.stl
mechanical_design/STL/Lock Housing - Lock Housing.stl
mechanical_design/STL/Outer Shell - Upper Z Lim Bracket.stl
mechanical_design/STL/Proposal_box - Battery Holder.stl
mechanical_design/STL/Proposal_box - Iris Stepper Block.stl
mechanical_design/STL/Proposal_box - Z Carriage Bracket.stl
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

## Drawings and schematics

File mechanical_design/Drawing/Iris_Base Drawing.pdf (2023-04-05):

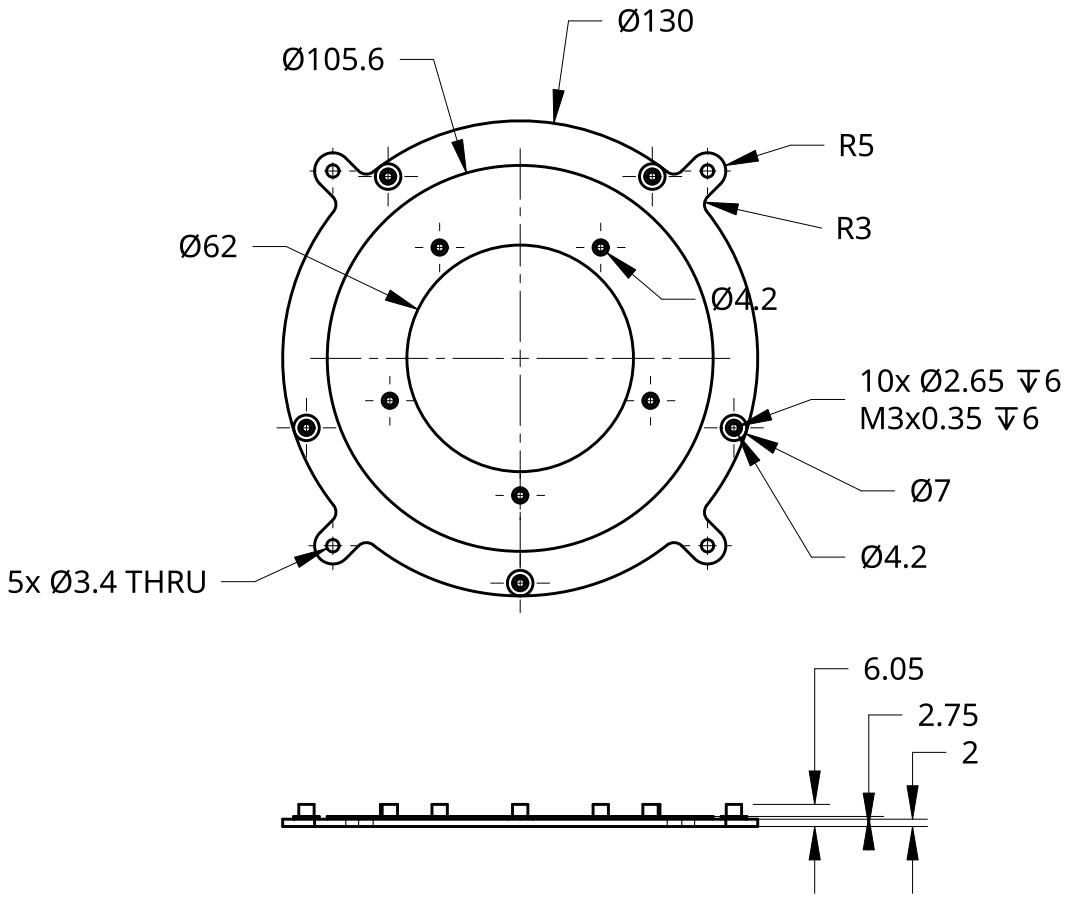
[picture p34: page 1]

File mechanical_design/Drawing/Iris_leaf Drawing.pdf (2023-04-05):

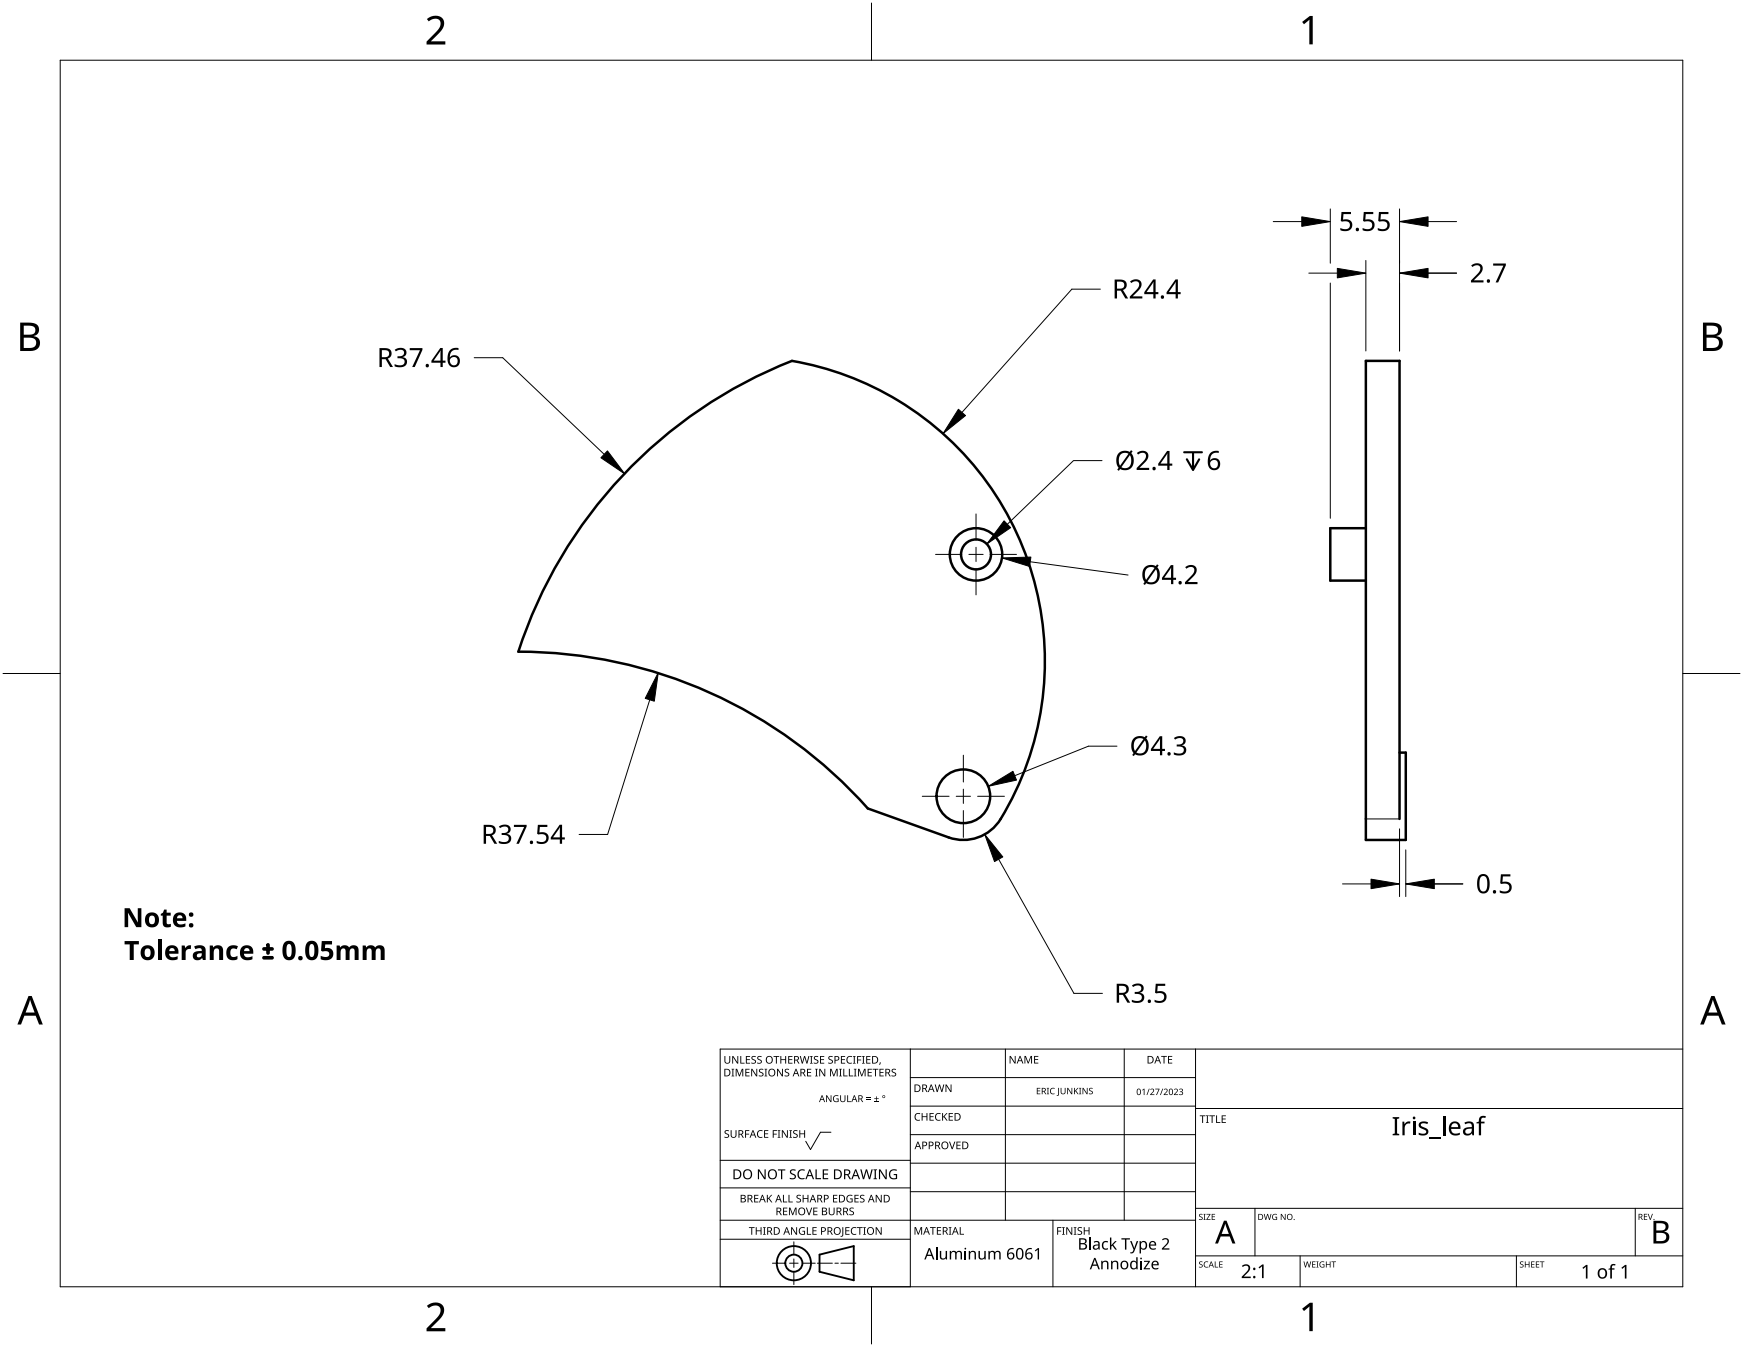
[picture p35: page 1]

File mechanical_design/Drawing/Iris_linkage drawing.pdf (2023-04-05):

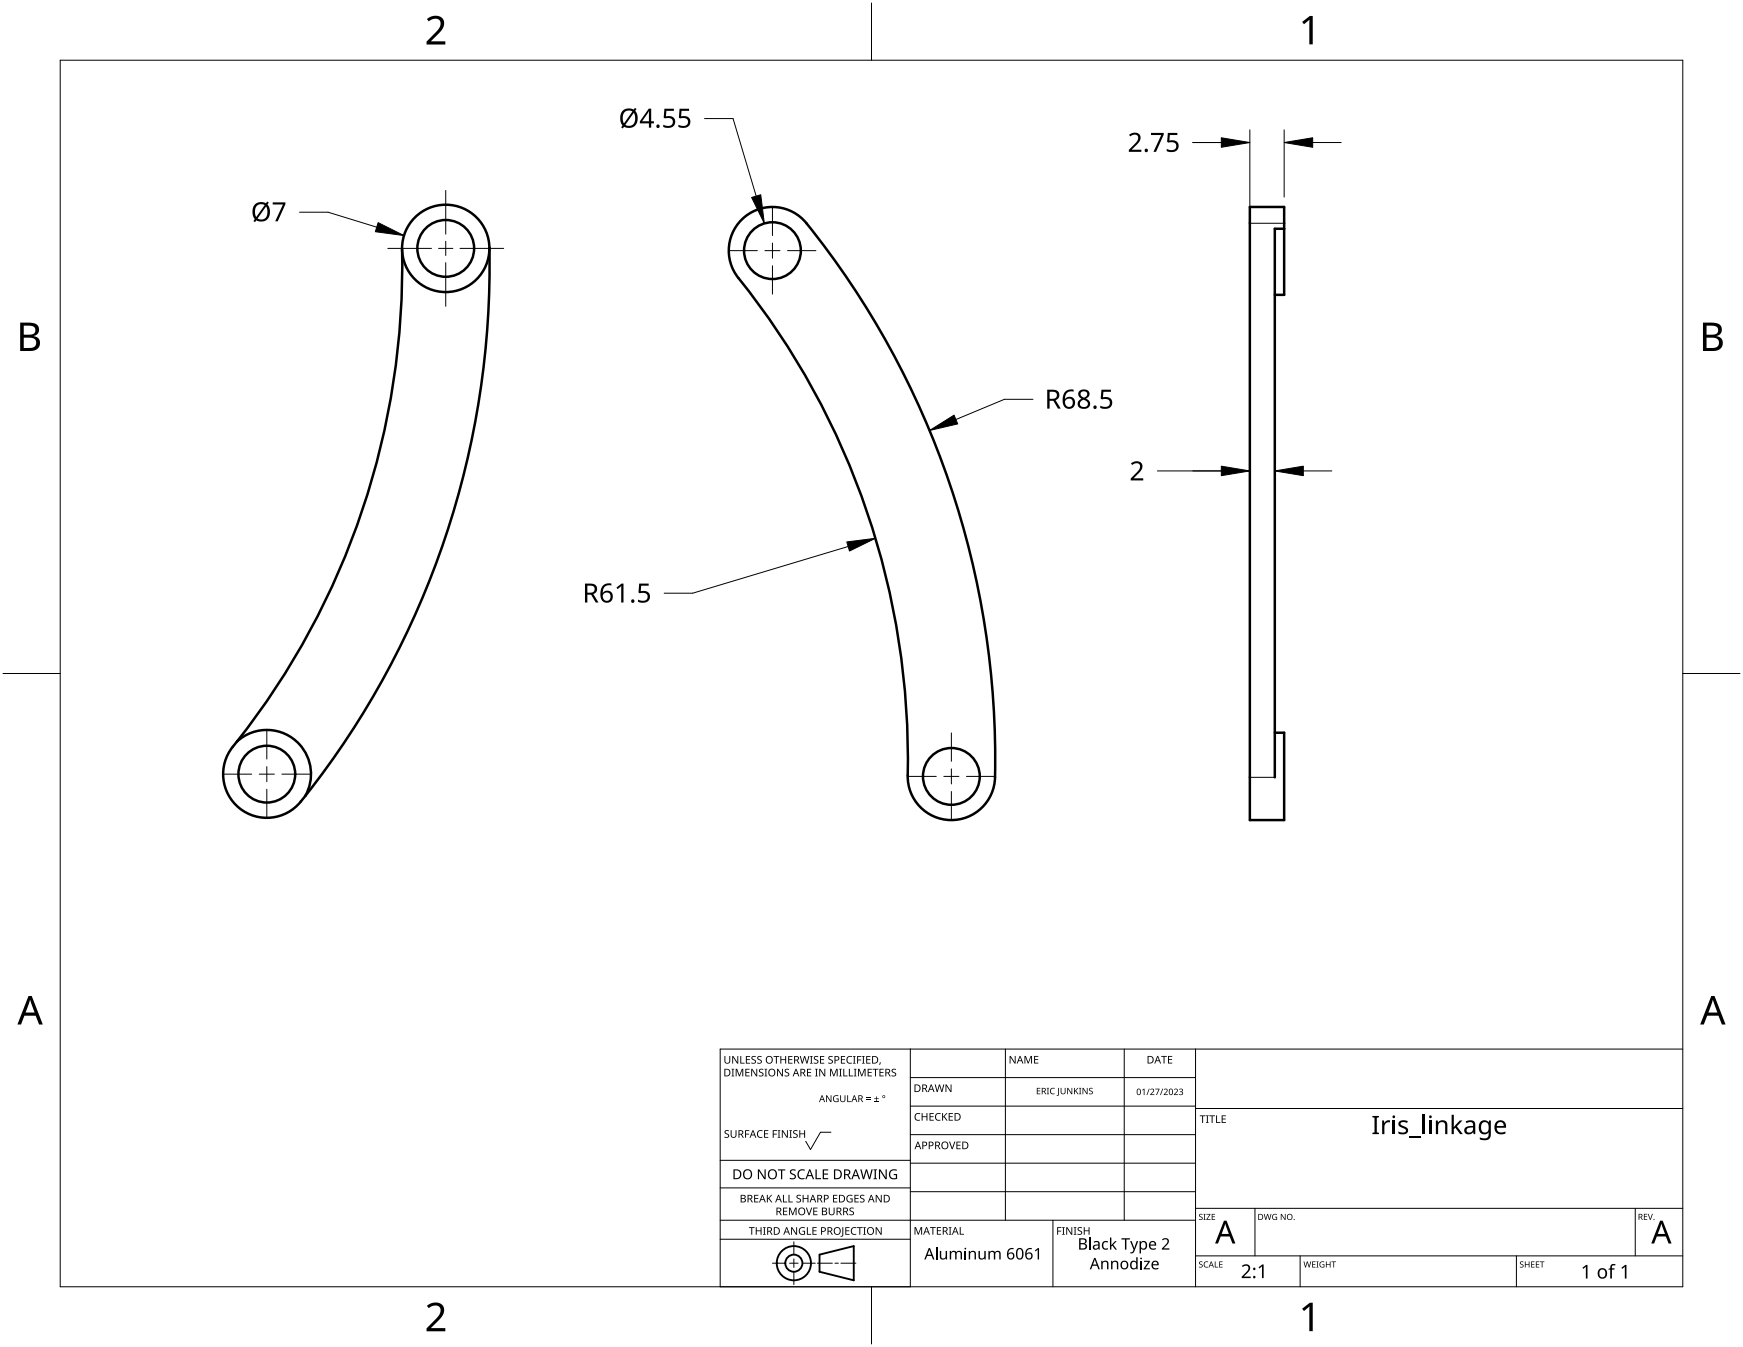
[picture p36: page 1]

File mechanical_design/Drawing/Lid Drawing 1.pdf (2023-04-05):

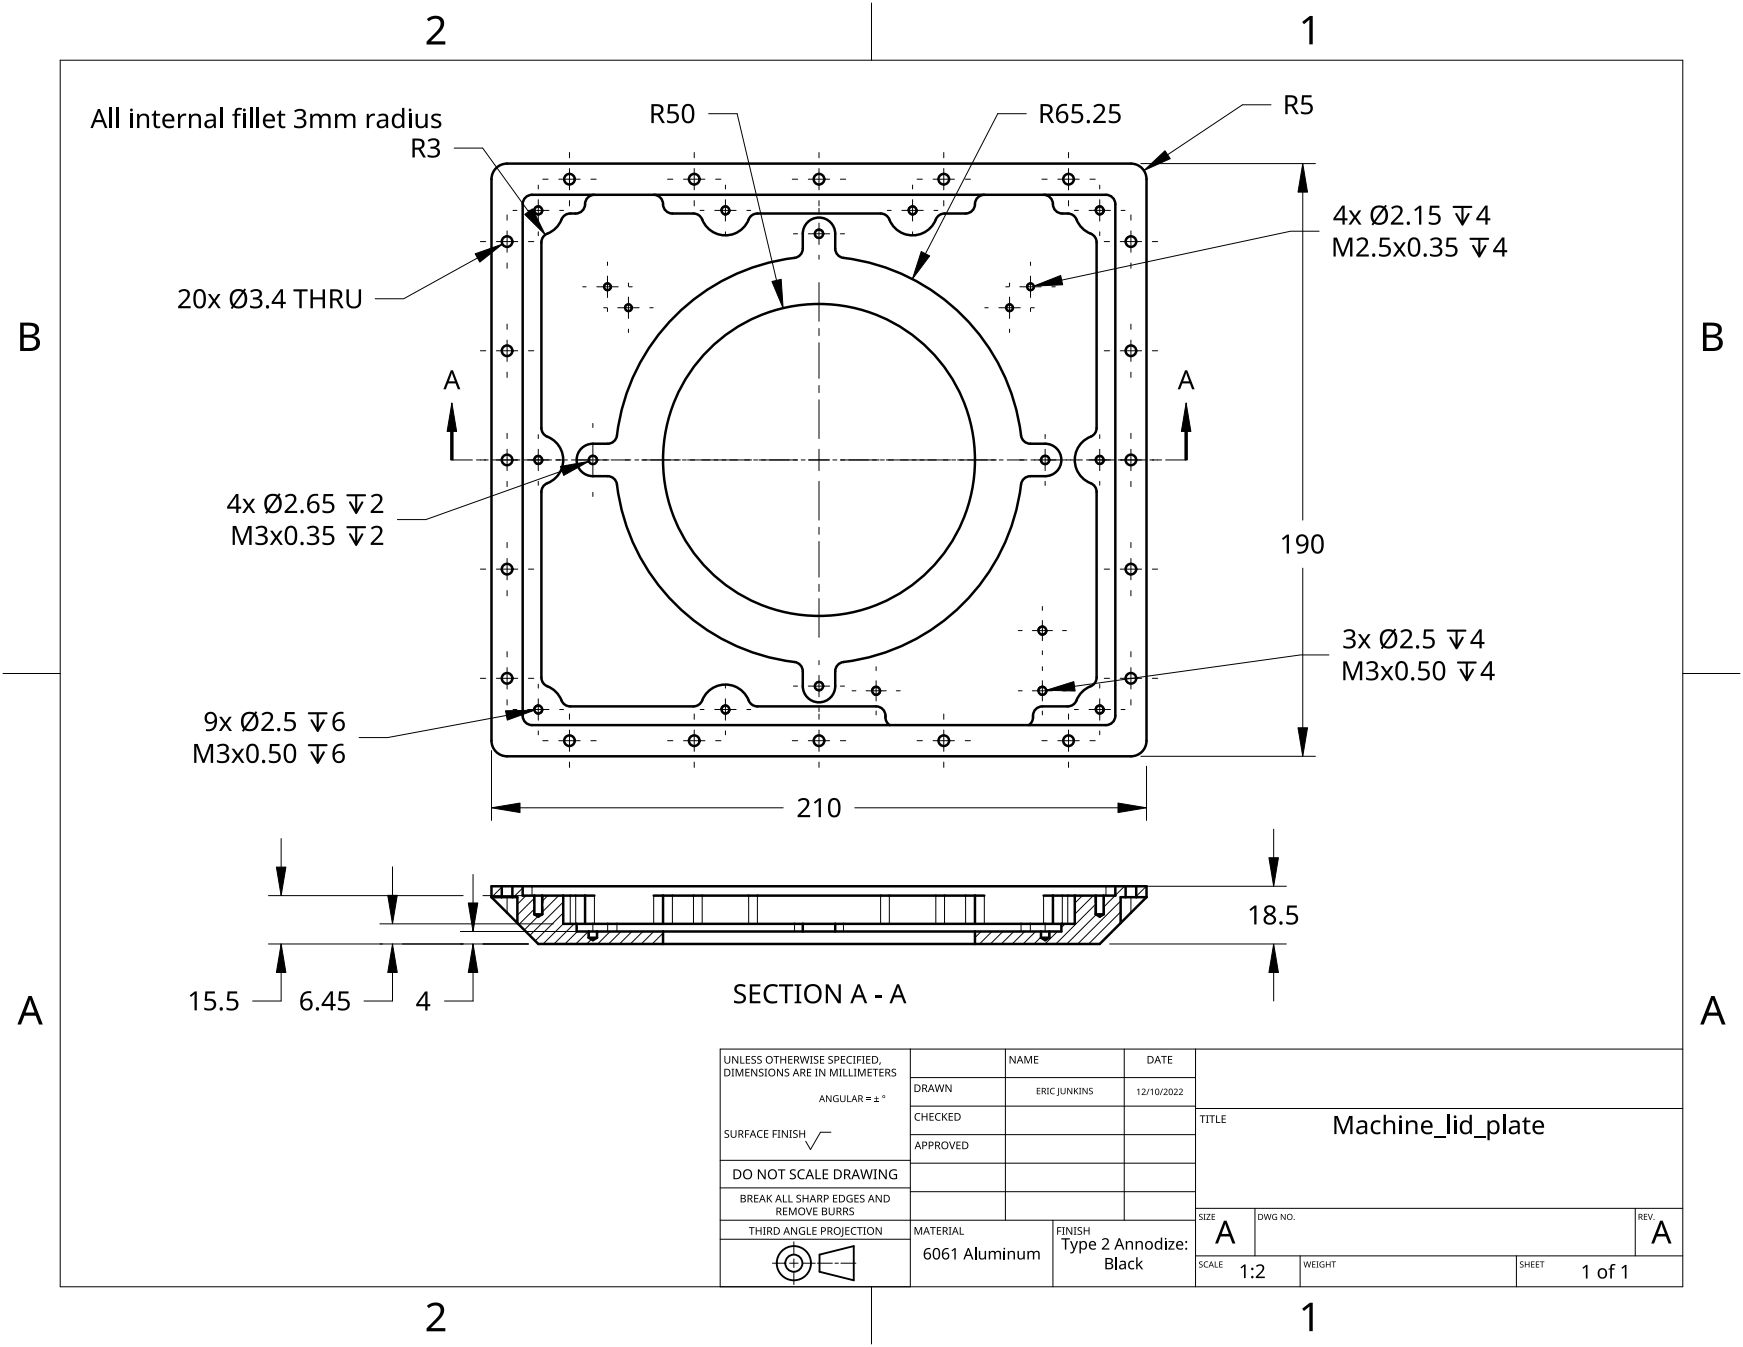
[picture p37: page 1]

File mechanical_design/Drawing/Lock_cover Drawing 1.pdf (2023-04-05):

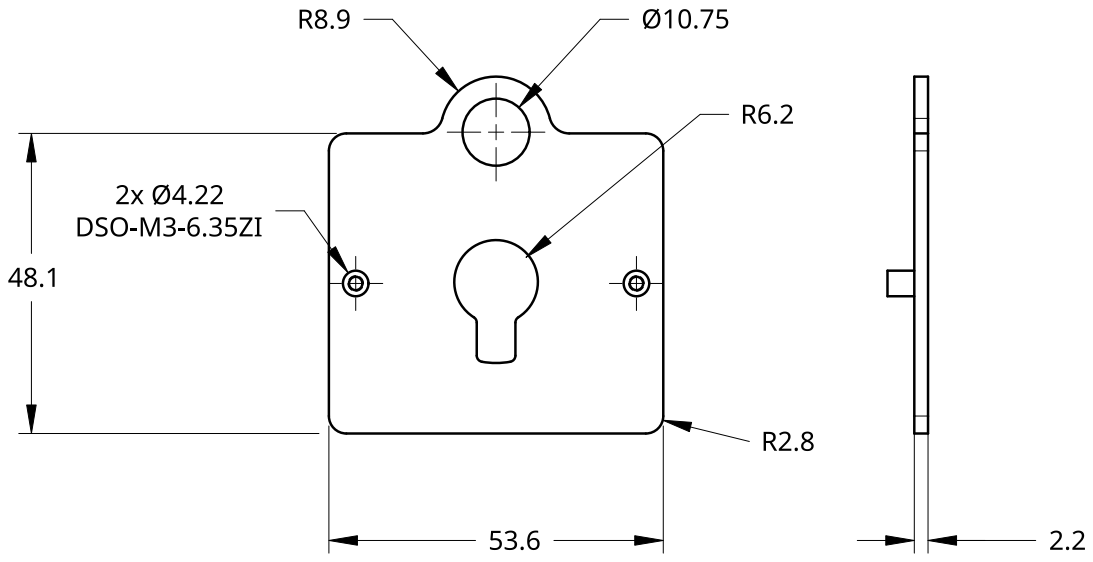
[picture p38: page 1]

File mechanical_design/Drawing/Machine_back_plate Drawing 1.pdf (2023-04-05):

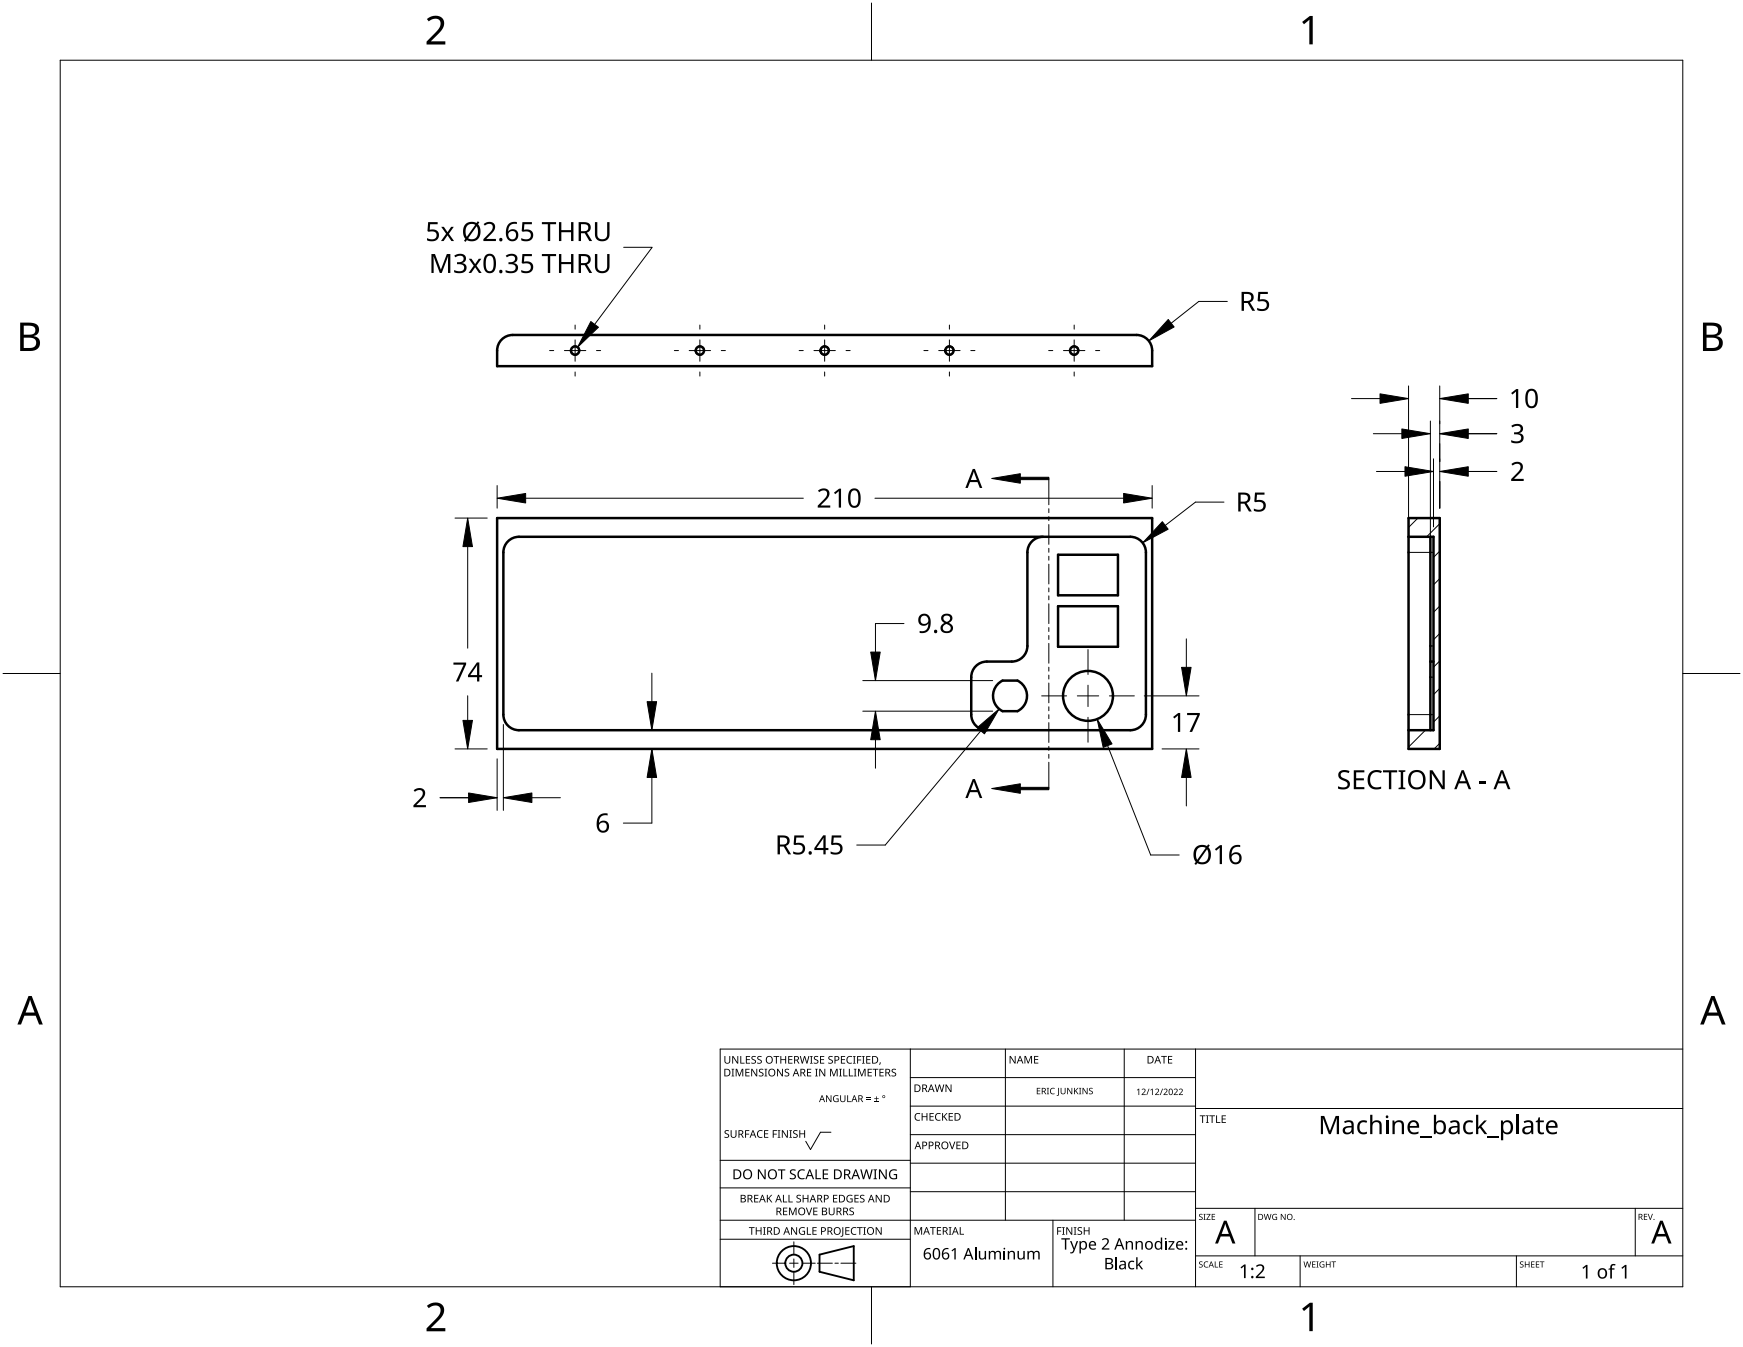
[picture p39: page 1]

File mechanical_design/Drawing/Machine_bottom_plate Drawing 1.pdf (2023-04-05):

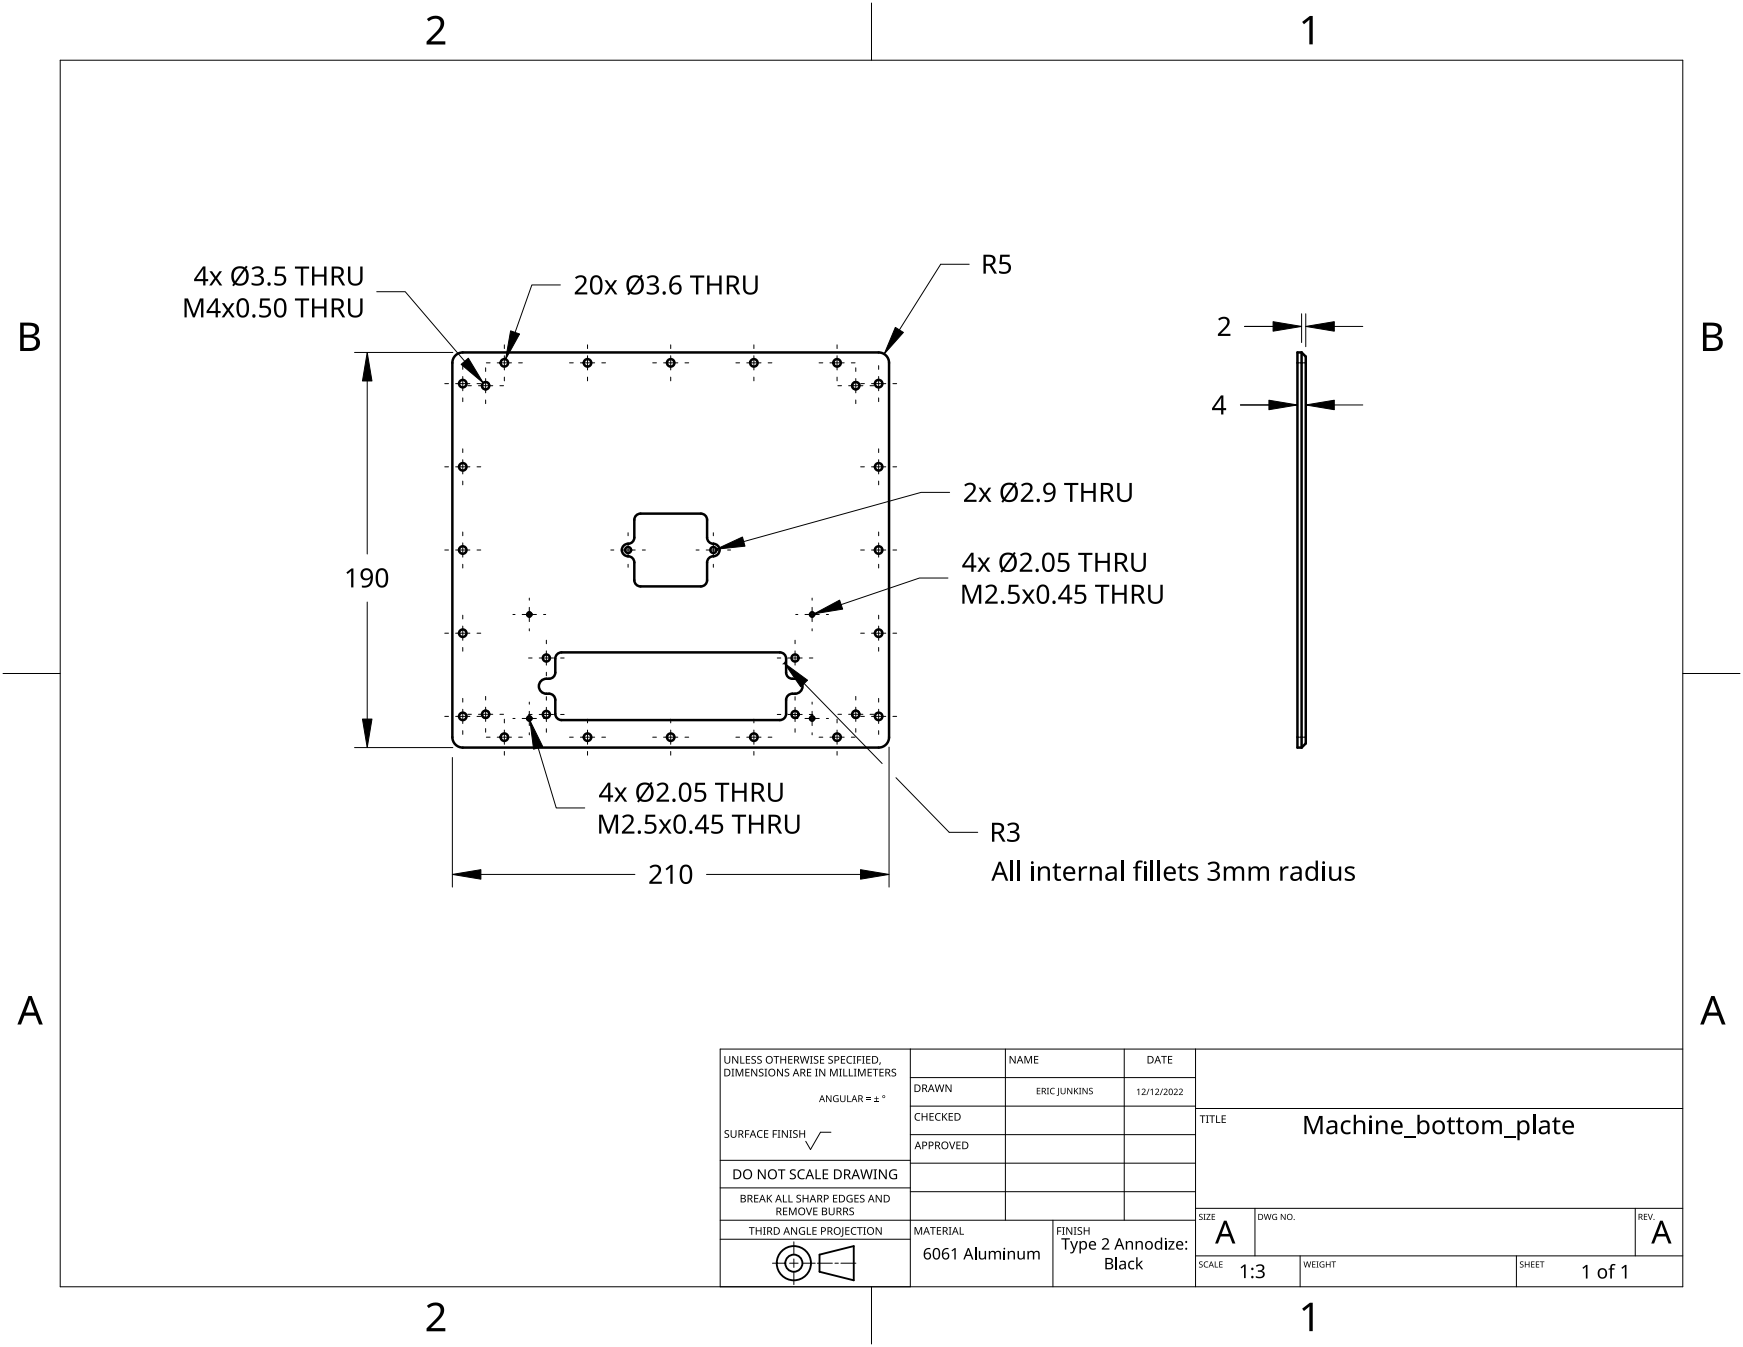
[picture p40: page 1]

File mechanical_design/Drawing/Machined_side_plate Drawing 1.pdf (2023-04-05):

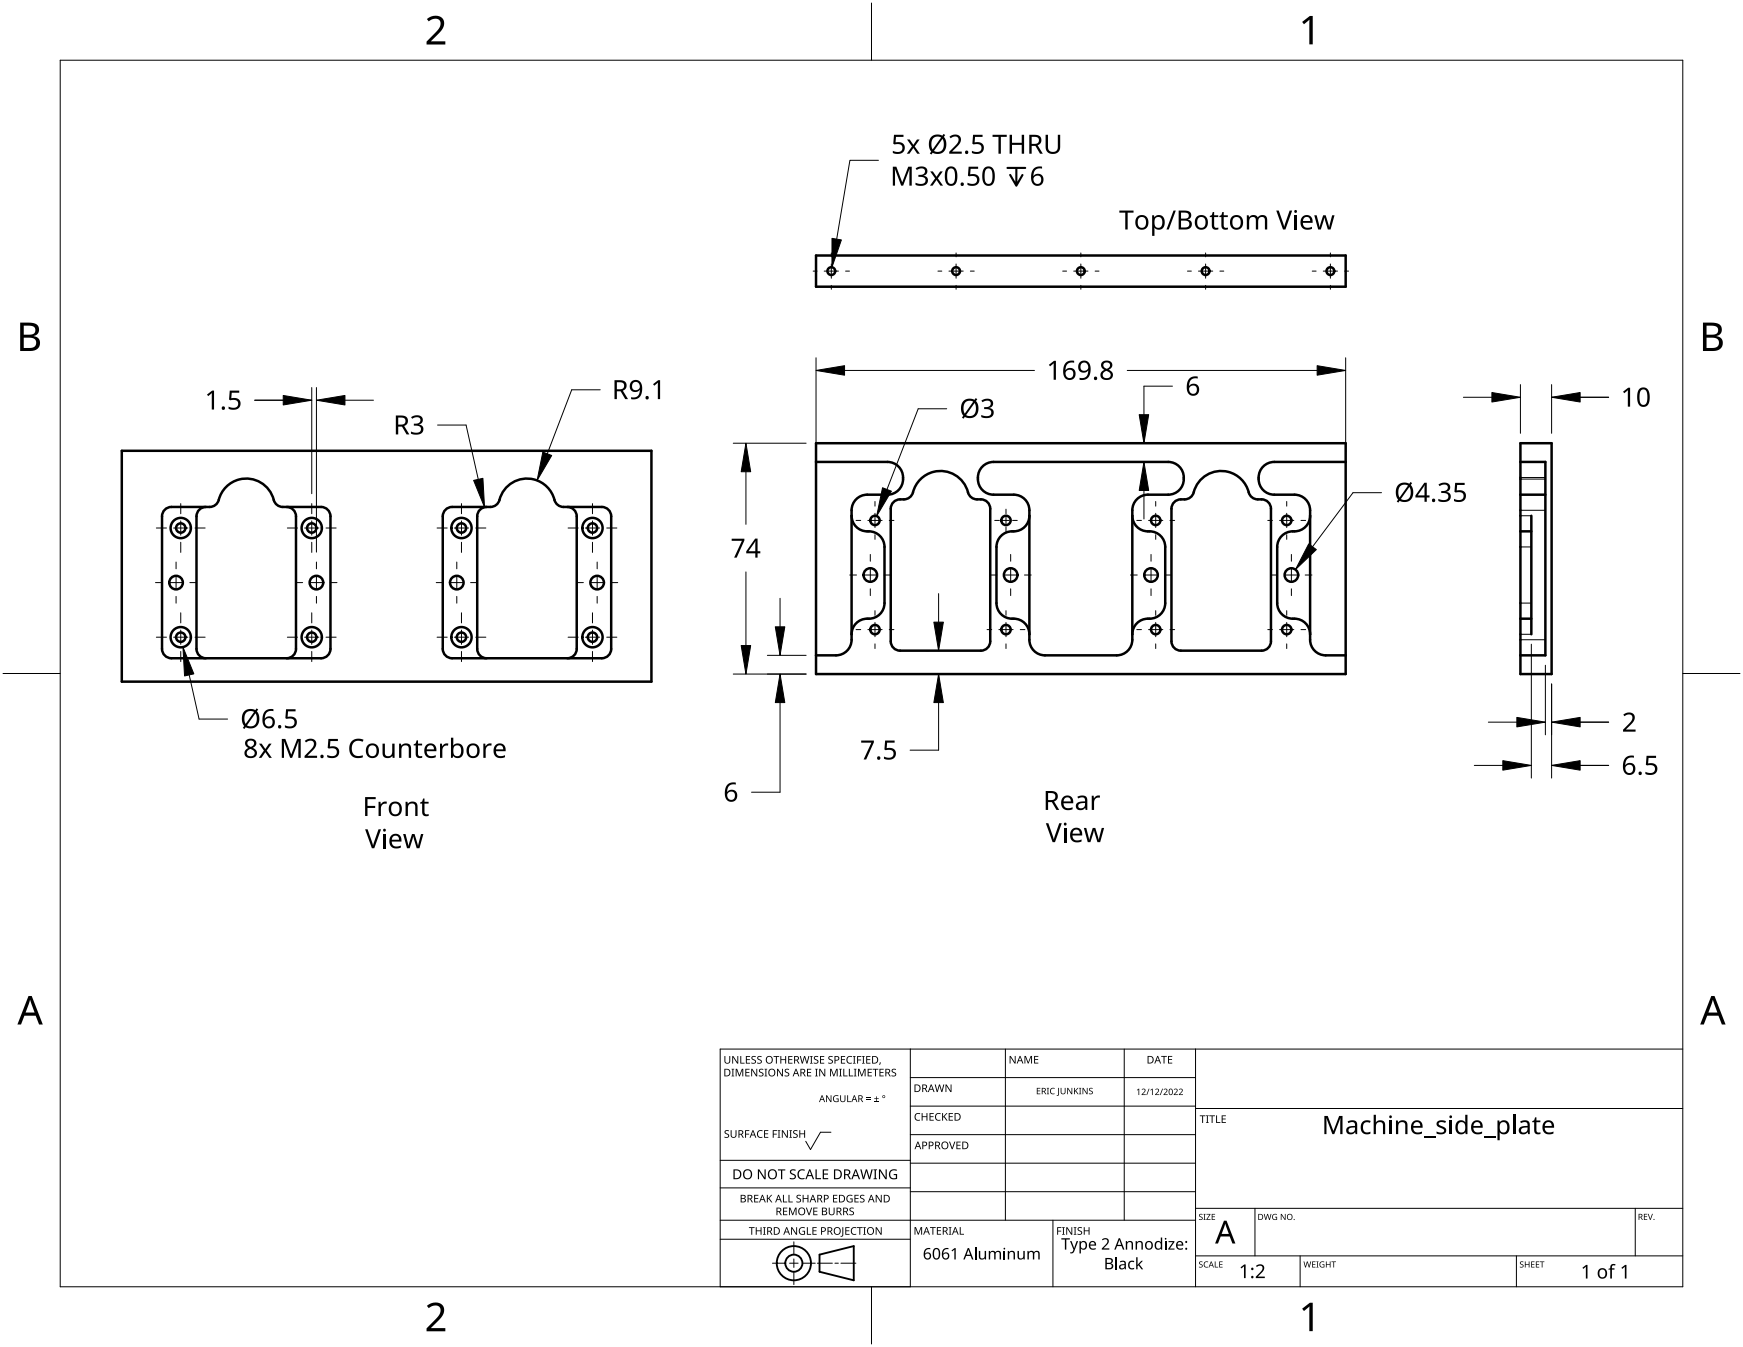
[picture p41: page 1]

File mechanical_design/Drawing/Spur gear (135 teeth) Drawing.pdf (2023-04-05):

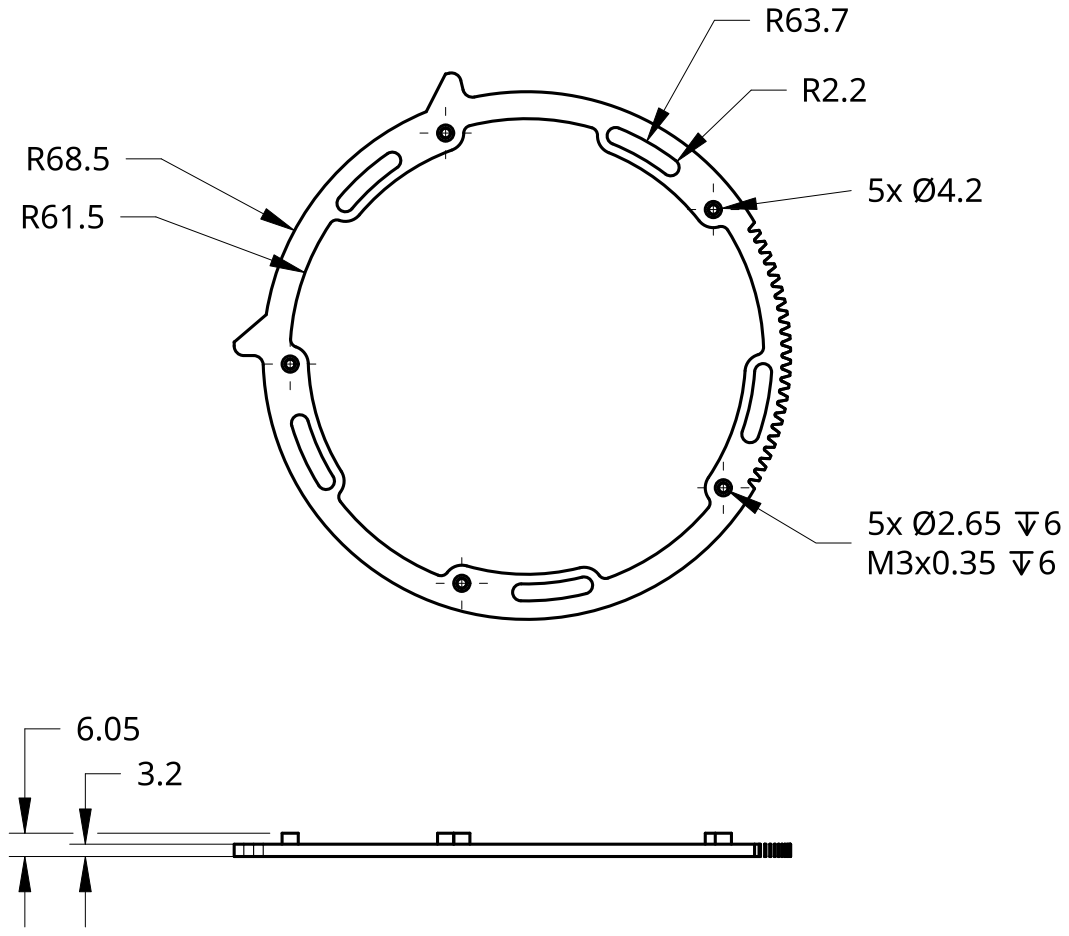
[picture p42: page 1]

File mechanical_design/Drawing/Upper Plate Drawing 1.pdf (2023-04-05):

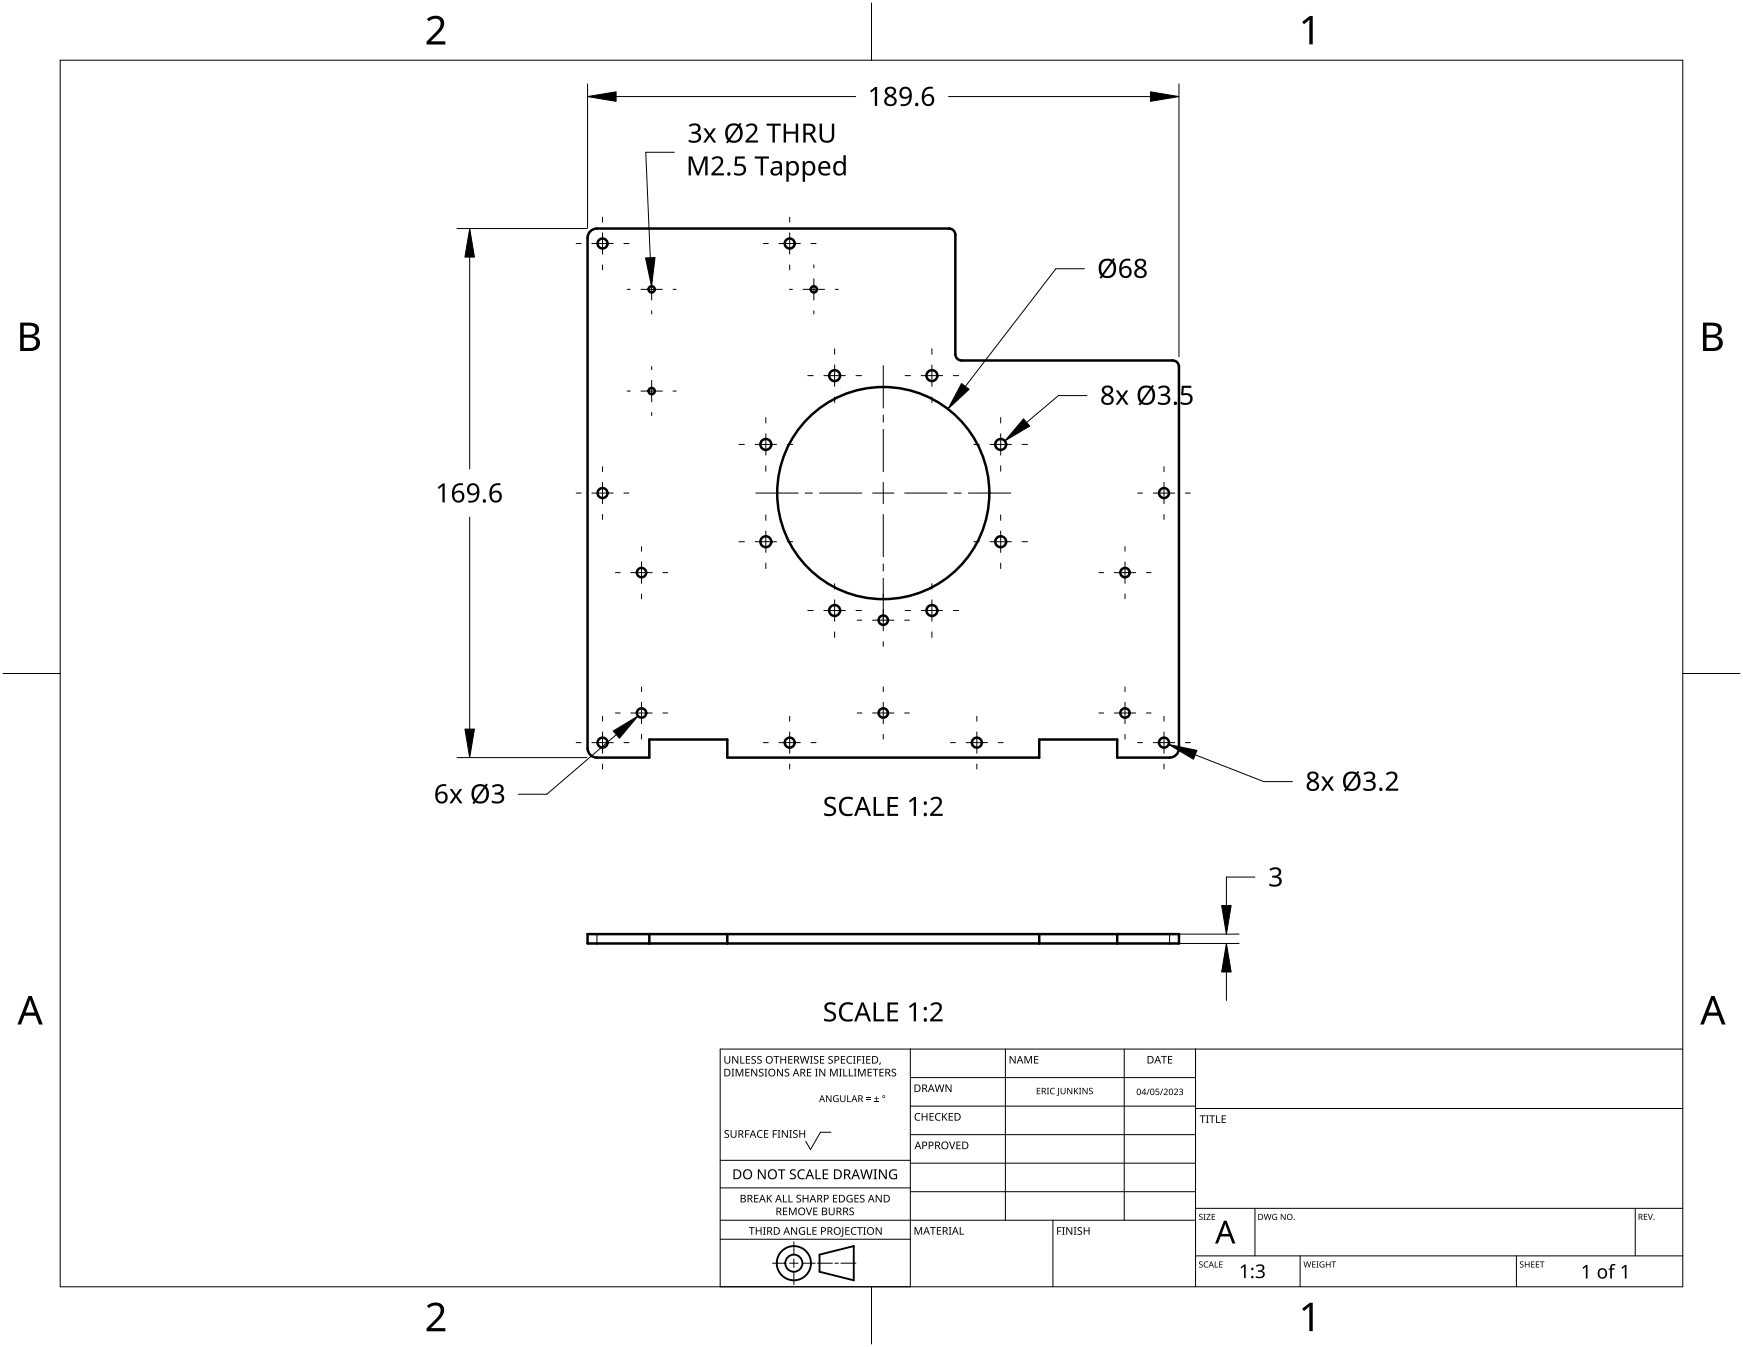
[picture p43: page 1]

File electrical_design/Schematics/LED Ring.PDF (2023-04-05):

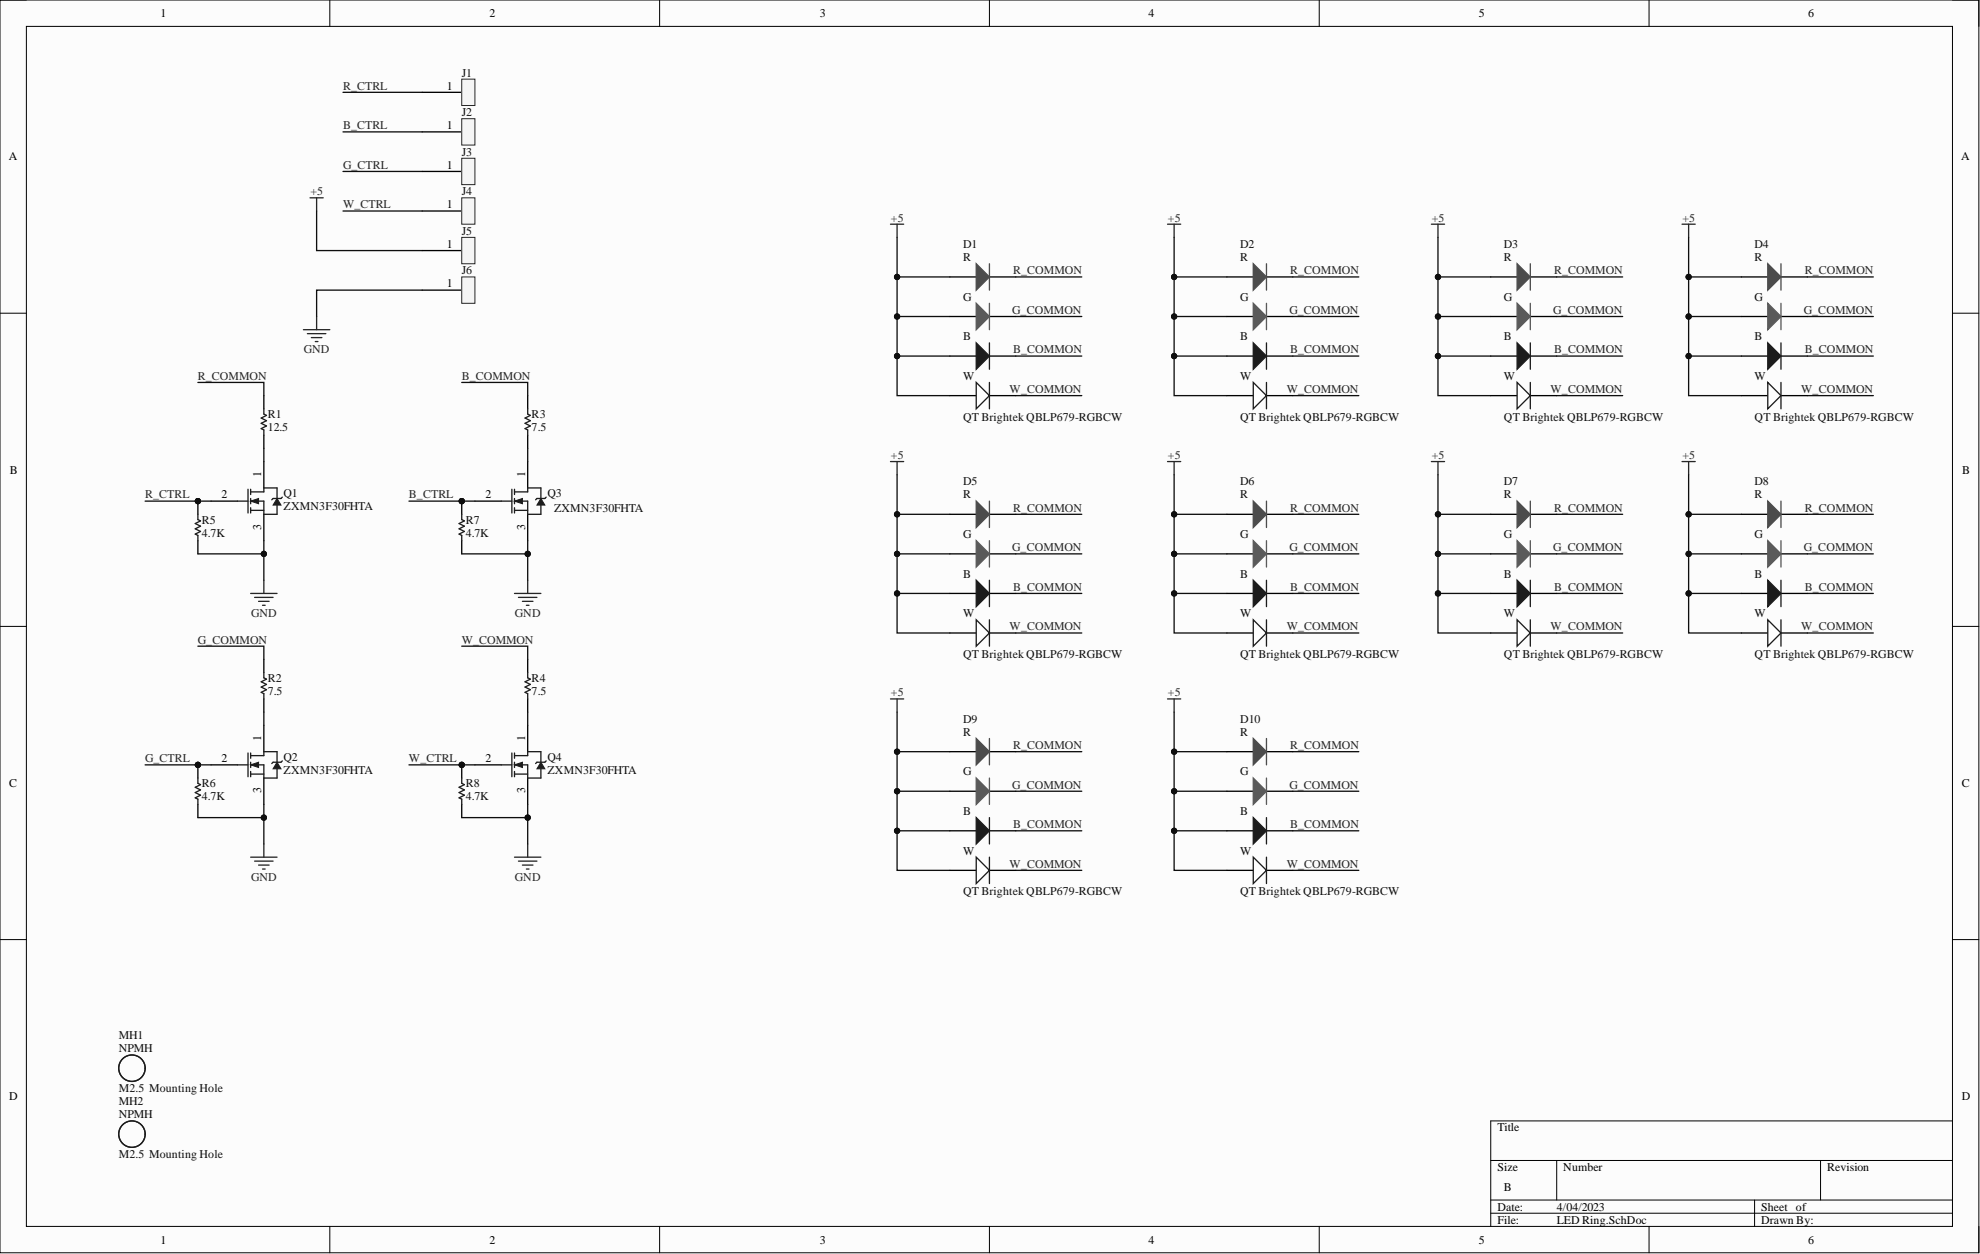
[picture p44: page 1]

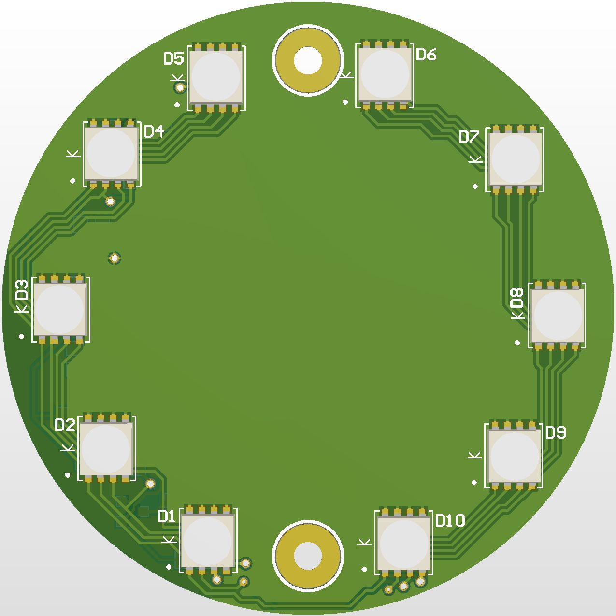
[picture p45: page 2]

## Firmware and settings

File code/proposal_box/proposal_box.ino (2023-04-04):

#include <LiquidCrystal.h>
#include <math.h>
#include <TMCStepper.h>         // TMCstepper - https://github.com/teemuatlut/TMCStepper
#include <SoftwareSerial.h>     // Software serial for the UART to TMC2209 - https://www.arduino.cc/en/Reference/softwareSerial
#include <Streaming.h>          // For serial debugging output - https://www.arduino.cc/reference/en/libraries/streaming/
#include "Arduino.h"
#include "SoftwareSerial.h"
#include "DFRobotDFPlayerMini.h"

#define OPEN 1
#define BUZZER 2
#define UNLOCK 3

#define IRIS_TX         3   
#define IRIS_RX         2   
#define THETA_RX        4 
#define THETA_TX        5 
#define Z_RX            6 
#define Z_TX            7
#define LOCK_4_READ_PIN 8
#define EXT_LED_4       9
#define LOCK_3_READ_PIN 12
#define EXT_LED_3       13
#define DIR_Z           27
#define DIR_THETA       29
#define DIR_IRIS        31
#define IRIS_LIM_HIGH   33
#define STATE_RESET     34
#define IRIS_LIM_LOW    35
#define RED             41
#define GREEN           43
#define BLUE            45
#define WHITE           47
#define Z_LIM_HIGH      (55)
#define Z_LIM_LOW       (56)
#define LOCK_1_READ_PIN (60)
#define LOCK_2_READ_PIN (61)
#define EXT_LED_1       (66)
#define EXT_LED_2       (68)

#define THETA_VEL 1000
#define IRIS_VEL 500
#define Z_VEL 1000

#define DRIVER_ADDRESS   0b00
#define R_SENSE 0.11f  

//int Z_LIM_HIGH = PIN_A1;
//int Z_LIM_LOW = PIN_A2;
//int LOCK_1_READ_PIN = PIN_A6;
//int LOCK_2_READ_PIN = PIN_A7;
//int EXT_LED_1 = PIN_A12;
//int EXT_LED_2 = PIN_A14;

SoftwareSerial iris_serial(IRIS_RX, IRIS_TX);
SoftwareSerial theta_serial(THETA_RX, THETA_TX);
SoftwareSerial z_serial(Z_RX, Z_TX);
TMC2209Stepper iris_driver(&iris_serial, R_SENSE, DRIVER_ADDRESS); 
TMC2209Stepper theta_driver(&theta_serial, R_SENSE, DRIVER_ADDRESS); 
TMC2209Stepper z_driver(&z_serial, R_SENSE, DRIVER_ADDRESS); 

SoftwareSerial speaker_serial(10, 11); // RX, TX
DFRobotDFPlayerMini player;
void printDetail(uint8_t type, int value);

const int rs = 44, en=42, d4=48, d5=46,d3=50,d2=52;
LiquidCrystal lcd(rs, en, d5, d4, d3, d2);

int counter=0;
int lock_state=0;
int main_state=0;
int z_state=0;
int iris_state=0;


void set_lock_status(int lock_num, int state){
  int lock_1_pos = 9;
  int lock_2_pos = 14;
  switch(lock_num){
    case 0:
      lcd.setCursor(lock_1_pos, 0);
      break;
    case 1:
      lcd.setCursor(lock_2_pos, 0);
      break;
    case 2:
      lcd.setCursor(lock_1_pos, 1);
      break;
    case 3:
      lcd.setCursor(lock_2_pos, 1);
      break;
    default:
      break;
  }
  lcd.print(state ? "*" : " ");
  
}

void lock_reset(){
  lock_state = 0;
  player.volume(22);
  player.play(BUZZER);
  delay(1000);
  lcd_start_state();
  write_leds();
}

void next_lock_level(){
  delay(100);
  player.volume(25);
  player.play(UNLOCK);
  delay(100);
  set_lock_status(lock_state, 1);
  lock_state +=1;
  write_leds();
}

void write_leds(){
  int pin = 0;

  switch(lock_state){
    case 0:
      digitalWrite(EXT_LED_1, LOW);
      digitalWrite(EXT_LED_2, LOW);
      digitalWrite(EXT_LED_3, LOW);
      digitalWrite(EXT_LED_4, LOW);
      break;
    case 1:
      digitalWrite(EXT_LED_1, HIGH);
      break;
    case 2:
      digitalWrite(EXT_LED_2, HIGH);
      break;
    case 3:
      digitalWrite(EXT_LED_3, HIGH);
      break;
    case 4:
      digitalWrite(EXT_LED_4, HIGH);
      break;
    default:
      break;
    
  }
}

int build_lock_state(){
  int l1 = digitalRead(LOCK_1_READ_PIN);
  int l2 = digitalRead(LOCK_2_READ_PIN);
  int l3 = digitalRead(LOCK_3_READ_PIN);
  int l4 = digitalRead(LOCK_4_READ_PIN);
  if (l1 + l2 + l3 + l4 > 1){
     lock_reset();
     return -1;
  }
  return l1 + (l2 << 1) + (l3 << 2) + (l4 << 3);
}

void play_opening_message(){
  int scroll_time = 3000;
  lcd.clear();
  lcd.setCursor(0,0);
  lcd.print("Congratulations");
  lcd.setCursor(0,1);
  lcd.print("on solving the");
  delay(scroll_time);
  lcd.clear();
  lcd.setCursor(0,0);
  lcd.print("on solving the");
  lcd.setCursor(0,1);
  lcd.print("puzzle Annie...");
  delay(scroll_time + 2000);
  lcd.clear();
  lcd.setCursor(0,0);
  lcd.print("puzzle Annie...");
  lcd.setCursor(0,1);
  lcd.print("Now are you ready");
  delay(scroll_time);
  lcd.clear();
  lcd.setCursor(0,0);
  lcd.print("Now are you ready");
  lcd.setCursor(0,1);
  lcd.print("for the next");
  delay(scroll_time);
  lcd.clear();
  lcd.setCursor(0,0);
  lcd.print("for the next");
  lcd.setCursor(0,1);
  lcd.print("adventure?");
//  delay(scroll_time);
//  lcd.clear();
//  lcd.setCursor(0,0);
//  lcd.write((uint8_t)0);
}

void read_locks(){
  int sound_delay = 20;
  int state_val = build_lock_state();

  switch(lock_state){
    case -1:
      //Do nothing
      break;
    case 0:
      if (state_val == 1){
        next_lock_level();
      } else if (state_val) {
        lock_reset();
      }
      break;
    case 1:
      if (state_val != 0 && (state_val >= 2 && state_val <= 3)){
        next_lock_level();
      } else if (state_val > 3){
        lock_reset();
      }
      break;
    case 2:
      if (state_val != 0 && (state_val >= 4 && state_val <= 7)){
        next_lock_level();
      } else if (state_val > 7){
        lock_reset();
      }
      break;
    case 3:
      if (state_val != 0 && (state_val >= 8 && state_val <= 15)){
        next_lock_level();
        digitalWrite(WHITE, HIGH);
        digitalWrite(BLUE, HIGH);
        delay(1000);
        player.volume(27);
        player.play(OPEN);
        main_state = 1;
      } else if (state_val > 15){
        lock_reset();
      }
      break;
    default:
      break;
  }
}

void lcd_start_state(){
  lcd.setCursor(0,0);
  lcd.print("Locks   [ ]  [ ]");
  lcd.setCursor(0,1);
  lcd.print("Status  [ ]  [ ]");

  for (int i=0; i<4; i++){
    set_lock_status(i, 0);
  }
}

void initialize_speaker(){
  speaker_serial.begin(9600);
  Serial.println();
  Serial.println(F("Initializing DFPlayer ... (May take 3~5 seconds)"));

  if (!player.begin(speaker_serial)) {  //Use softwareSerial to communicate with mp3.
    Serial.println(F("Unable to begin:"));
    Serial.println(F("1.Please recheck the connection!"));
    Serial.println(F("2.Please insert the SD card!"));
    while(true);
  }
  Serial.println(F("DFPlayer Mini online."));

  player.volume(0);  //Set volume value. From 0 to 30
}

void initialize_lcd(){
  Serial.println("Initializing LCD screen...");
  lcd.begin(16,2);
  lcd.setCursor(0,0);
  lcd.print("Begin Initialize..");

  byte customChar[8] = {
      0b01110,
      0b00100,
      0b01110,
      0b10001,
      0b10001,
      0b10001,
      0b01110,
      0b00000
  };
  lcd.createChar(0, customChar);
  
  Serial.println("LCD screen started sucessfully!");  
}

void initialize_steppers(){
  Serial.println("Initializing Stepper drivers...");
  iris_serial.begin(11520);           // initialize software serial for UART motor control
  iris_driver.beginSerial(11520);      // Initialize UART
  iris_driver.begin();                 // UART: Init SW UART (if selected) with default 115200 baudrate
  iris_driver.toff(5);                 // Enables driver in software
  iris_driver.rms_current(1000);        // Set motor RMS current
  iris_driver.microsteps(64);         // Set microsteps
  iris_driver.en_spreadCycle(false);
  iris_driver.pwm_autoscale(true);     // Needed for stealthChop

  Serial.println("Sucessfully started iris stepper driver!");

  theta_serial.begin(11520);           // initialize software serial for UART motor control
  theta_driver.beginSerial(11520);      // Initialize UART
  theta_driver.begin();                 // UART: Init SW UART (if selected) with default 115200 baudrate
  theta_driver.toff(5);                 // Enables driver in software
  theta_driver.rms_current(1000);        // Set motor RMS current
  theta_driver.microsteps(64);         // Set microsteps
  theta_driver.en_spreadCycle(false);
  theta_driver.pwm_autoscale(true);     // Needed for stealthChop

  Serial.println("Sucessfully started theta stepper driver!");

  z_serial.begin(11520);           // initialize software serial for UART motor control
  z_driver.beginSerial(11520);      // Initialize UART
  z_driver.begin();                 // UART: Init SW UART (if selected) with default 115200 baudrate
  z_driver.toff(5);                 // Enables driver in software
  z_driver.rms_current(2000);        // Set motor RMS current
  z_driver.microsteps(64);         // Set microsteps
  z_driver.en_spreadCycle(false);
  z_driver.pwm_autoscale(true);     // Needed for stealthChop

  Serial.println("Sucessfully started z stepper driver!");
}

void initialize_io(){
  Serial.println("Initializing all I/O...");
  pinMode(LED_BUILTIN, OUTPUT);
  pinMode(LOCK_1_READ_PIN, INPUT);
  pinMode(LOCK_2_READ_PIN, INPUT);
  pinMode(LOCK_3_READ_PIN, INPUT);
  pinMode(LOCK_4_READ_PIN, INPUT);

  pinMode(Z_LIM_LOW, INPUT);
  pinMode(Z_LIM_HIGH, INPUT);
  pinMode(IRIS_LIM_LOW, INPUT);
  pinMode(IRIS_LIM_HIGH, INPUT);
  
  pinMode(STATE_RESET, INPUT);
  
  pinMode(EXT_LED_1, OUTPUT);
  pinMode(EXT_LED_2, OUTPUT);
  pinMode(EXT_LED_3, OUTPUT);
  pinMode(EXT_LED_4, OUTPUT);

  pinMode(WHITE, OUTPUT);
  pinMode(RED, OUTPUT);
  pinMode(GREEN, OUTPUT);
  pinMode(BLUE, OUTPUT);
}

void initialize_iris_position(){
  if(!digitalRead(IRIS_LIM_LOW)){
    Serial.println("Iris not in intial closed State, setting now");
    iris_driver.shaft(0);
    iris_driver.VACTUAL(500);
    while(!digitalRead(IRIS_LIM_LOW)){
      //do nothing
    }
    delay(150);
    iris_driver.VACTUAL(0);
  }
  iris_state=0;
}

void initialize_z(){
  if (!digitalRead(Z_LIM_LOW)){
    Serial.println("Z not in initial low state, setting now");
    z_driver.shaft(0);
    z_driver.VACTUAL(500);
    while(!digitalRead(Z_LIM_LOW)){
      //do nothing
    }
    delay(150);
    z_driver.VACTUAL(0);
  }
  z_state = 0;
}

void cycle_iris(){
  switch(iris_state){
    case 0:
      //Iris fully closed
      Serial.println("Beginning opening iris");
      iris_driver.shaft(1);
      iris_driver.VACTUAL(500);
      iris_state = 1;
      break;
    case 1:
      //currently opening
      if (digitalRead(IRIS_LIM_HIGH)){
        Serial.println("Iris fully opened!");
        delay(150);
        iris_driver.VACTUAL(0);
        iris_state = 2;
      }
      break;
    case 2:
      //Is fully opened
      Serial.println("Beginning closing iris");
      iris_driver.shaft(0);
      iris_driver.VACTUAL(500);
      iris_state = 3;
      break;
    case 3:
      if (digitalRead(IRIS_LIM_LOW)){
        Serial.println("Iris fully closed!");
        delay(150);
        iris_driver.VACTUAL(0);
        iris_state = 0;
      }
      break;
    default:
      break;
  }
}

void cycle_z(){
  switch(z_state){
    case 0:
      Serial.println("Beginning Z up");
      z_driver.shaft(1);
      z_driver.VACTUAL(1000);
      z_state = 1;
      break;
    case 1:
      if (digitalRead(Z_LIM_HIGH)){
        Serial.println("High triggered");
        delay(150);
        z_driver.VACTUAL(0);
        z_state = 2;
      }
      break;
    case 2:
      Serial.println("Beginning Z down");
      z_driver.shaft(0);
      z_driver.VACTUAL(1000);
      z_state = 3;
      break;
    case 3:
      if (digitalRead(Z_LIM_LOW)){
        Serial.println("Low triggered");
        delay(150);
        z_driver.VACTUAL(0);
        z_state = 0;
      }
      break;
    default:
      break;
  }
}



void opening_routine(){
  
  //Start spinning the Theta motor
  switch(main_state){
    case 0:
      theta_driver.VACTUAL(0);
      digitalWrite(WHITE, HIGH);
      digitalWrite(BLUE, HIGH);
    case 1:
      //Start spinning theta motor, and start opening the iris
      theta_driver.shaft(0);
      theta_driver.VACTUAL(1000);
      Serial.println("Beginning opening iris");
      iris_driver.shaft(1);
      iris_driver.VACTUAL(500);
      main_state = 2;
      break;
    case 2:
      if (digitalRead(IRIS_LIM_HIGH)){
        Serial.println("Iris fully opened!");
        delay(150);
        iris_driver.VACTUAL(0);
        main_state = 3;
      }
      break;
    case 3:
      Serial.println("Starting Z Up now");
      z_driver.shaft(1);
      z_driver.VACTUAL(1000);
      delay(150);
      main_state = 4;
      break;
    case 4:
      if (digitalRead(Z_LIM_HIGH)){
        Serial.println("Z at the top");
        delay(150);
        z_driver.VACTUAL(0);
        main_state = 5;
        delay(1000);
      }
      break;
    case 5:
      if (digitalRead(STATE_RESET)){
        reset_all();
      }
//      z_driver.shaft(0);
//      z_driver.VACTUAL(1000);
      break;
    case 6:
      
      break;
//    case 6:
//      if (digitalRead(Z_LIM_LOW)){
//        delay(150);
//        z_driver.VACTUAL(0);
//        main_state = 7;
//      }
//      break;
//    case 7:
//      iris_driver.shaft(0);
//      iris_driver.VACTUAL(500);
//      main_state = 8;
//      break;
//    case 8:
//      if (digitalRead(IRIS_LIM_LOW)){
//        delay(150);
//        iris_driver.VACTUAL(0);
//        main_state = 1;
//        delay(500);
//      }
//      break;
    default:
      break;
  }
}

void reset_all(){
  digitalWrite(WHITE, LOW);
  digitalWrite(BLUE, LOW);
  digitalWrite(RED, LOW);
  digitalWrite(GREEN, LOW);
  theta_driver.VACTUAL(0);
  initialize_z();
  initialize_iris_position();
  main_state = 0;
  lcd_start_state();
  lock_state = 0;
}

void pwm_led(){
  if (counter <= 200){
    digitalWrite(GREEN, HIGH);
  } else if (counter <=400){
    digitalWrite(GREEN,LOW);
  } else if (counter <= 600) {
    digitalWrite(RED, HIGH);
  } else if (counter <= 800){
    digitalWrite(RED, LOW);
    counter = 0;
  }
}

void setup() {
  // put your setup code here, to run once:
  Serial.begin(9600);
  initialize_lcd();
  initialize_io();
  initialize_speaker();
  initialize_steppers();
  lcd_start_state();
  initialize_z();
  initialize_iris_position();
 Serial.println("Ready to start up!");
  delay(500);

}
1



void loop() {

  if (main_state == 0){
    read_locks();
  } else {
    opening_routine();
}

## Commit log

2023-04-05 Adding electrical design files
    [LED Ring.step]
2023-04-05 Adding mechanical files
    [Battery Clip Vertical - Cover Plate.stl, Iris V2 - Base.step, Iris V2 - Leaf.step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]
2023-04-13 Adding readme, and BOM files
    [Proposal BOM - Consolidated BOM.csv]
